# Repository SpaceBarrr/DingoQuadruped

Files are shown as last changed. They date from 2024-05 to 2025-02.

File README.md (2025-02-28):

# Kelpie Quadruped

<p align="center">
    
</p>

## Overview
This repository hosts the code for the Kelpie Quadruped, a robot designed to be low-cost yet capable of both education and research usage and being extensively modified with additional actuators and sensors. CAD for the Kelpie can be found [here](https://grabcad.com/library/kelpie-quadruped-1). A full bill of materials for purchasable components can be found within this repo.
A brief overview of the Kelpie can be found [here](https://www.youtube.com/watch?v=VYclMd-JAFM&ab_channel=SpaceBar).

This code is based on the [Dingo Quadruped](https://github.com/MonashRobotics/DingoQuadruped) codebases, with extensive modifications, including integration into ROS 1 Noetic.

The repository includes a driver node, dingo_driver.py, which should be used anytime the code is run. This file enables joystick control of the Dingo, and allows joint and/or task space commands generated by any other code to be passed through the driver via the appropriate ROS command topics. The joystick can also be toggled on and off to override commands received via ROS command topics

The repo also includes a WeBots simulation of the Kelpie, based on URDF file and meshes which are also provided.

## How Kelpie ROS Network Works
The following flow diagram shows a simplified overview of how a joystick command is handled by the driver to affect joint movements:
<p align="center">
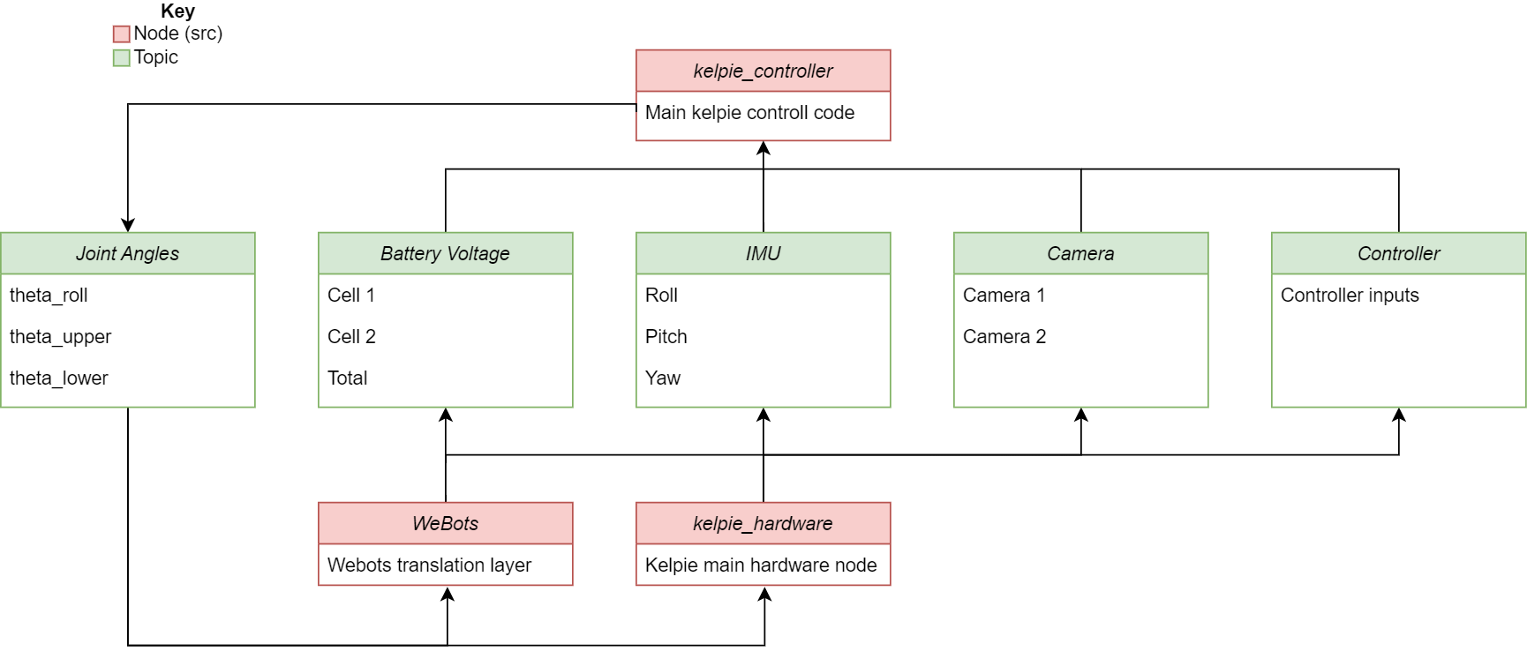
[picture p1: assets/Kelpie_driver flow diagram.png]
    
</p>

## Installation of Code
### Natively
- Install Ubuntu 20.04 onto the Pi's SD card via the [Raspberry Pi Imager](https://www.raspberrypi.com/software/), and setup username, password and network information.
- Install [ros-noetic](http://wiki.ros.org/noetic/Installation/Ubuntu)
- Install necessary packages via `sudo apt-get install python3-catkin-tools git python3-rosdep python3-rosinstall python3-rosinstall-generator python3-wstool python3-pip build-essential wireless-tools libraspberrypi-bin ros-noetic-joy ros-noetic-catkin python3-catkin-tools i2c-tools libi2c-dev python3-smbus`
- Install necessary python packages via `pip install spidev transforms3d pillow rpi.gpio pyserial simple-pid`
- Change directory to the home folder: `cd ~`
- Get a list of available time zones: `timedatectl list-timezones`
- Set local time zone from list e.g: `sudo timedatectl set-timezone Australia/Melbourne`
- Clone this (the Kelpie Quadruped) repository using git: `git clone ...`
- Update all submodules: `git submodule update --init`
- Move into the kelpie_ws folder: `cd /DingoQuadruped/kelpie_ws`
- Initialise rosdep: `sudo rosdep init`
- Fetch dependencies with rosdep: `rosdep update`
- Build the workspace: `catkin build`
- Source the workspace: `source devel/setup.bash`
- Set ROS_MASTER_URI: `echo "export ROS_MASTER_URI=http://dingo:11311" >> ~/.bashrc`
- Source ROS in bashrc .bashrc:`echo "source /opt/ros/noetic/setup.bash" >> ~/.bashrc`, `source ~/.bashrc`
- (Optional) Add a line to .bashrc to automatically source the workspace: `echo "source ~/DingoQuadruped/kelpie_ws/devel/setup.bash" >> ~/.bashrc`, `source ~/.bashrc`

### Additional Installation Steps
#### Bluetooth Setup
For getting bluetooth controller working (for instance PS4 controller)
- More info here: https://www.makeuseof.com/manage-bluetooth-linux-with-bluetoothctl/
- Install bluetooth: 
    - `sudo apt-get install bluetooth bluez bluez-tools`
    - `sudo apt-get install pi-bluetooth`
- To pair and connect a controller:
    - `bluetoothctl`
    - `scan on`
    - `trust AA:BB:CC:11:22:33` (example device)
    - `pair AA:BB:CC:11:22:33` 
    - `connect AA:BB:CC:11:22:33`
- To test the controller:
    - `jstest /dev/input/js0`
- To list connected devices:
    - `bluetoothctl paired-devices`
- To later forget the controller:
    - `bluetoothctl remove AA:BB:CC:11:22:33`

At this stage, the controller will only connect if you run `bluetoothctl` in the terminal, and then press the pair button on the controller. To bypass the step of running `bluetoothctl`, do the following:
- Create a shell script called connect_controller.sh (Make a note of where you create it) with the following contents:
```.
#!/bin/bash

# Replace 'XX:XX:XX:XX:XX:XX' with your controller's MAC address
controller_mac="XX:XX:XX:XX:XX:XX"

# Use bluetoothctl to connect the controller
bluetoothctl <<EOF
connect $controller_mac
exit
EOF`
```
- Make it executable by running `chmod +x connect_controller.sh`
- Create a UDEV rule to run this script every time the controller attempts to pair: `SUBSYSTEM=="bluetooth", KERNEL=="hci0", ACTION=="add", ENV{DEVTYPE}=="adapter", TAG+="systemd", SYMLINK+="bluetooth", RUN+="/bin/sleep 10", RUN+="/path/to/connect_controller.sh"`
- reload the UDEV rules: `sudo udevadm control --reload`
The controller should now autopair every time the pair button is pressed, without needing to do anything on the Pi

#### Wifi Setup
To get WiFi working
- Edit the file /etc/netplan/50-cloud-init.yaml 
- Add the following to the bottom of the file
```.   
    wifis:
        wlan0:
            optional: true
            dhcp4: true
            access-points:
                "<wifi SSID>":
                    password: "<wifi password>"
```

#### LCD Node Additional Setup
The LCD node has been created following the waveshare tutorial here: https://www.waveshare.com/wiki/1.47inch_LCD_Module. Apart from installing the libraries listed there, the fonts also need to be moved into the ubuntu fonts folder to be used by executing the following lines:
- `cd ~`
- `sudo apt-get install unzip -y`
- `sudo wget https://files.waveshare.com/upload/8/8d/LCD_Module_RPI_code.zip`
- `sudo unzip ./LCD_Module_RPI_code.zip`
- `cd ~/LCD_Module_RPI_code/RaspberryPi/python/Font`
- `sudo mv Font00.ttf /usr/share/fonts/truetype/Font00.ttf`
- `sudo mv Font01.ttf /usr/share/fonts/truetype/Font01.ttf`
- `sudo mv Font02.ttf /usr/share/fonts/truetype/Font02.ttf`

If getting an error with "rounded_rectangle", need to install later version of Pillow.
- Upgrade pillow with `pip3 install --upgrade Pillow`

#### Setting necessary permissions for ROS
To run ROS as non-root, must set permissions correctly via udev for several /dev files.
- Add the following to /etc/udev/rules.d/99-ROS.rules
```.   
       KERNEL=="ttyS0", OWNER="root", GROUP="ros", MODE="0660"
       KERNEL=="spi", OWNER="root", GROUP="ros", MODE="0660"
       KERNEL=="i2c", OWNER="root", GROUP="ros", MODE="0660"
       KERNEL=="gpiomem", OWNER="root", GROUP="ros", MODE="0660"
       KERNEL=="mem", OWNER="root", GROUP="ros", MODE="0660"
```
- Add new group to user account: `sudo groupadd ros && sudo adduser <username> ros`
- Reload udev rules: `sudo udevadm control --reload-rules && sudo udevadm trigger`

#### Setting up I2C
- First, run this command to check whether i2c is working for root: `sudo i2cdetect -y 1`. If this doesnt work, try replacing the 1 with a 0. If this works, replace the 1 with a 0 in all subsequent steps.
- Now try for your user: `i2cdetect -y 1`. If the same matrix appears, all is good. Otherwise, run the following:
```.
    sudo groupadd i2c
    sudo chown :i2c /dev/i2c-1
    sudo chmod g+rw /dev/i2c-1
    sudo usermod -aG i2c [INSERT YOUR USERNAME]
```
- Reboot or logout and back in and then check if i2c is working by running `i2cdetect -y 1`. The matrix should now appear for your user.

#### Setting up SPI
Please run the code first before following these steps. If you do not receive an SPI permission error, there is no need to do the following SPI setup steps. Proceed if you receive an error
- Run `ls -la /dev/spidev*` to list SPI devices
- Then, run the following to give your user SPI permissions, repeating the last two lines for all SPI devices listed from previous command:
```.
    sudo groupadd spi
    sudo usermod -aG spi <yourusername>
    sudo chown :spi <put the spi device name here>
    sudo chmod g+rw <put the spi device name here>
```
- Try running the code again. If it works, reboot the device and run the code again immediately after logging in. If it still works after reboot, no need to continue, but it if does not, keep going below:
- Run `sudo nano /etc/systemd/system/spi-permissions.service` and put the following into the file, saving and exiting afterwards:
```.
    [Unit]
    Description=Set SPI Permissions
     
    [Service]
    ExecStart=/path/to/your/script.sh
    User=root
    Group=root
    Restart=on-failure
    RestartSec=5s
     
    [Install]
    WantedBy=multi-user.target
```
- Now, run `nano ~/startspi.sh` and put the following into the file, saving and exiting afterwards. Note: If your SPI device names are different, please update them accordingly:
```.
    #!/bin/bash
    sudo usermod -aG spi <yourusername>
    sudo chown :spi /dev/spidev0.0
    sudo chmod g+rw /dev/spidev0.0
    sudo chown :spi /dev/spidev0.1
    sudo chmod g+rw /dev/spidev0.1
```
- Run the following in the terminal:
    - `sudo chmod +x /path/to/your/script.sh`
    - `sudo systemctl daemon-reload`
    - `sudo systemctl enable spi-permissions.service`
    - `sudo systemctl start spi-permissions.service`

SPI should now work across restarts

#### Setting up Voltage Monitoring
The voltage monitoring on this robot was done using the TLA2024IRUGT chip. Please install the required library to run it with `pip3 install adafruit-circuitpython-tla202x`

#### Setting up camera
- Install required packages: `sudo apt-get install ros-noetic-video-stream-opencv`

#### Configuring web server
- Install apache `sudo apt-get install apache2
`
- Start apache `sudo /etc/init.d/apache2 start`
- Edit the apache conf to point to the Kelpie HTML files and allow access `sudo nano /etc/apache2/sites-enabled/000-default.conf`
    - Change `/var/www` to `home/{username}/DingoQuadruped/web_gui/`
    - Add in the directory directives to allow access
        ```
        <Directory home/{username}/DingoQuadruped/web_gui>
            Options Indexes FollowSymLinks
            AllowOverride All
            Require all granted
        </Directory>
        ```
- Restart apache `sudo /etc/init.d/apache2 restart`
- Install ROS bridge `sudo apt-get install ros-noetic-rosbridge-suite`
- Finally, the web server should be accessible on the local network at http://dingo:80/index.html

#### SD Card Backup
It's a good idea to backup the sdcard every so often. Here is how to do that on linux.
- Take out the sdcard from the Raspberry Pi and mount it into another linux system.
- Run these commands to backup/restore. Replace source/destination appropriately.
    - Backup to file: `sudo dd if=/dev/sdb of=~/kelpie_backup.img bs=4M status=progress`
    - Restore back to sdcard: `sudo dd if=kelpie_backup of=/dev/sdb bs=4M status=progress`

#### Servo Calibration
Help with getting the servos calibrated
 - Run the `calibrate_servo.py` file in the following path: `kelpie_ws\src\kelpie_hardware_interface\scripts\calibrate_servo.py`
 - For auto calibration, type `auto`, this will calibrate all the legs automatically, excluding the roll servos
 - For manual calibration, type the servo name (e.g. `fr r` for front right, roll), then follow the instructions to fine tune the servos
 - Type `q` to save the quit the calibration script

## Running the code
### Kelpie_Driver
The Kelpie_Driver should be started before any other code is launched on the Kelpie. It starts joystick control of the robot and allows joint and task space commands to be received from other code or controllers via command ROS topics, as long as joystick control is disabled. If enabled, joystick control will override any commands sent through the command topics. To launch it, run the following line:
`roslaunch kelpie kelpie.launch`

Arguments are:
- mode (0/1)
    - 0: physical (default)
    - 1: simulation
- input_type (0/1): 
    - 0: PS4 controller (default)
    - 1: keyboard
- use_cam (0/1): 
    - 0: camera off (default)
    - 1: camera on (Note that this is induces lag on a Pi4, recommend Pi 5)

With no arguments specified, it will assume a joystick controller is used for control and it will launch the hardware interface with IMU feedback disabled. No joint data will be published for WeBots to use to simulate the robot.

As an example of how the arguments can be used, if the code is to be run with keyboard control and the camera enabled, you would launch the driver with the following arguments: 
`roslaunch kelpie kelpie.launch input_type:=1 use_cam:=1`

When the code is running, the device that is ssh'd into the Kelpie quadruped, you can go to http://dingo:80/index.html to access the gui.

### Kelpie Joystick Controls
<p align="center">
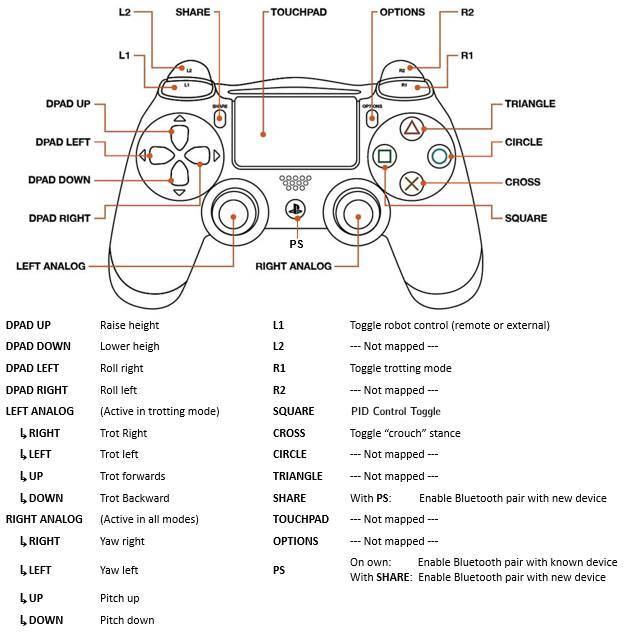
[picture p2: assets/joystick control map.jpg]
    
</p>

The diagram above shows the mapping of joystick commands for the Kelpie. These instructions are based on a PS4 type controller. An alternative, more general description of joystick commands is below:

The Kelpie has two main states: Rest and Trot. 
- While in the TROT state: Left stick controls the robot's movement. Right stick controls the robot's tilt and turning. PID control only applies to the yaw.
- While in the REST state: Left stick is disabled. Right stick controls the robot's gaze while staying in place. PID control can be toggled.

Buttons:
- Joystick Control Toggle (L1 Button): Pause/Resume control from the joystick.
- Gait Toggle (R1 Button): Toggles between trotting and resting modes.
- PID Control Toggle (Square): Toggles PID control on/off

Movement: (Speed proportional to how far stick is moved)
- Left Stick (Horizontal): Pushing left or right strafes the robot in that direction.
- Left Stick (Vertical): Push up to move forward, down to move backward.

Gaze:
- Right Stick (Horizontal): Pushing left or right turns the robot in that direction.
- Right Stick (Vertical): Push up to raise front of robot, down to raise back of robot.

Orientation:
- D-pad (Vertical): Pressing up or down adjusts the height of the robot.
- D-pad (Horizontal): Pressing left or right tilts the robot in that direction.

## Running the Simulation on WeBots
### For Windows users (Native Linux users can skip this)
- Install Windows Subsystem for Linux (WSL) for Ubuntu 20.04 by running `wsl --install -d Ubuntu-20.04` in your preferred terminal
- From Powershell, type in `wsl` (`wsl -d Ubuntu-20.04` if you have multiple ubuntu versions), this will launch WSL and Ubuntu 20.04

### Install Required Packages
- Execute the following in the bash terminal:
```
sudo apt-get update
sudo sh -c 'echo "deb http://packages.ros.org/ros/ubuntu $(lsb_release -sc) main" > /etc/apt/sources.list.d/ros-latest.list'
sudo apt install curl
curl -s https://raw.githubusercontent.com/ros/rosdistro/master/ros.asc | sudo apt-key add -
sudo apt-get update
sudo mkdir -p /etc/apt/keyrings
cd /etc/apt/keyrings
sudo wget -q https://cyberbotics.com/Cyberbotics.asc
echo "deb [arch=amd64 signed-by=/etc/apt/keyrings/Cyberbotics.asc] https://cyberbotics.com/debian binary-amd64/" | sudo tee /etc/apt/sources.list.d/Cyberbotics.list
sudo apt update
sudo apt install webots
sudo apt-get install ros-noetic-desktop-full ros-noetic-moveit
sudo apt-get install python3-rosdep
sudo rosdep init
rosdep update
sudo apt-get install ros-noetic-webots-ros ros-noetic-joy python3-pip
pip3 install transforms3d adafruit-circuitpython-servokit adafruit-circuitpython-bno055
sudo apt install python-is-python3
```
### Setting Up the Simulation Environment
- Source the ros files on the shell launch and other environment variables, **don't forget to change the file path** (make sure the path is WSL and not windows)
```
echo "source /opt/ros/noetic/setup.bash" >> ~/.bashrc
echo "export KELPIE_WS=/mnt/windows/path/to/kelpie_ws" >> ~/.bashrc
echo "export WEBOTS_HOME=/usr/local/webots" >> ~/.bashrc
source ~/.bashrc
```
- Set up the workspace
```
cd /path/to/kelpie_ws
catkin_make
```

### Running the Simulation Environment
- Run the kelpie launch file on a local ubuntu 20.04 environment.
```
cd /path/to/kelpie_ws
catkin_make
source devel/setup.bash
roslaunch src/kelpie/launch/kelpie.launch mode:=1
```
- Open another terminal and run the webots launch file
```
source devel/setup.bash
roslaunch src/kelpie_webots/launch/webots_ros_python.launch 
```

### Running the Simulation as a Digital Twin
- Connect to the kelpie and run it as described in [Kelpie_Driver](#kelpie_driver), in physical mode
```
roslaunch src/kelpie/launch/kelpie.launch mode:=0
```
- Run the webots launch file on your local (Ubuntu!) computer
```
cd /path/to/kelpie_ws
catkin_make
source devel/setup.bash
export ROS_MASTER_URI=http://dingo.local:11311/
roslaunch src/kelpie_webots/launch/webots_ros_python.launch 
```

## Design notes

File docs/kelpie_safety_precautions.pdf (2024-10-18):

# The Kelpie Safety Precautions

Manufacturing
- Do not touch the 3D printer nozzle when printing
- Be careful when taking off the supports from the 3D printed parts as they may be sharp

Operation
- Do not touch the servos when the robot it powered as it may get hot
- Avoid getting too close to the robot when in motion as you may get hit/pinched
- Do not use a LiPo battery when it is overcharged or undercharged

Storing
- Do not leave the LiPo battery in the robot when storing
- Always discharge the battery and store it in a safe location

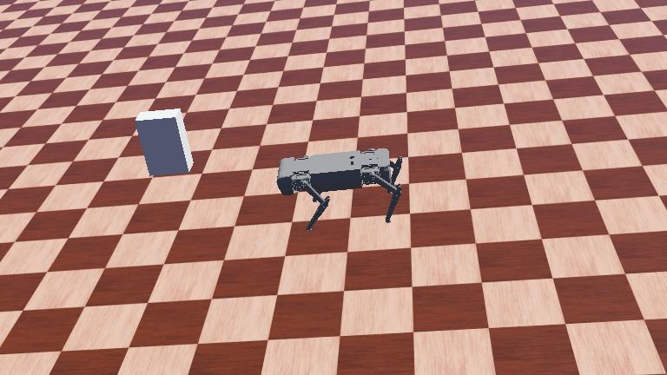
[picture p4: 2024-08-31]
kelpie_ws/src/kelpie_webots/launch/webots/worlds/.kelpie_default.jpg

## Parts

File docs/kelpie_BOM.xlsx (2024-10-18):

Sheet: Kelpie BOM
Category | Item | Link | Comments | Quantity | Price per item | Total Price
Leg Linkage Mechanism | Servo Motors | https://www.aliexpress.com/item/1005004670681332.html?spm=a2g0o.cart.0.0.35d338daLsP2P7&mp=1 | 180 degrees, 35kg | 12 | 44.48916667 | 533.87
 | Servo Horns | https://www.aliexpress.com/item/1005001485067326.html | RC Car Steering Servo Horn Arm 25T Teeth Long | 4 | 2.36 | 9.44
 | Servo Discs | https://www.aliexpress.com/item/32827000998.html?scm_id=1007.23125.137358.0&scm-url=1007.23125.137358.0 | 10 pcs, with screws. | 1 | 6.54 | 6.54
 | Heatsinks | https://vi.aliexpress.com/item/1005005848003793.html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 | Heat sinks for servos, cut in half for each | 4 | 0.38 | 1.52
 | Thermal tape | https://www.amazon.com.au/dp/B087D48T61?ref=ppx_pop_mob_ap_share | Thermal tape for servos, cut to size | 1 | 14.75 | 14.75
 | Threaded rods (Long) | https://www.aliexpress.com/item/1005004660730267.html?spm=a2g0o.detail.1000023.16.1569213ad8nkQv | M3 x 110mm (5pcs) | 1 | 1.26 | 1.26
 | Threaded rods,short | https://www.aliexpress.com/item/1005004660730267.html?spm=a2g0o.detail.1000023.16.1569213ad8nkQv | M3 x 25 (5pcs) | 1 | 1.14 | 1.14
 | Rod ends (Long) | https://www.aliexpress.com/item/32878321408.html?spm=a2g0o.detail.1000023.6.64cd339bFmvU9y | 10pcs, 015 M3 With Screw | 1 | 5.19 | 5.19
 | Rod ends (Short) | https://www.aliexpress.com/item/32878321408.html?spm=a2g0o.detail.1000023.6.64cd339bFmvU9y | 10pcs, 012 M3 With Screw | 1 | 5.19 | 5.19
 | Bearings | https://vi.aliexpress.com/item/1005007293843469.html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 | 10pcs, need 2pcs for each leg | 1 | 5.38 | 5.38
Computing | Raspberry Pi 4 Model B | https://core-electronics.com.au/raspberry-pi-4-model-b-8gb.html | 8gb Ram | 1 | 127.9 | 127.9
 | 32GB MicroSD card | https://core-electronics.com.au/microsd-memory-card-32gb-class-10.html | 32GB is maximum Pi supports | 1 | 19 | 19
 | LCD Screen | https://core-electronics.com.au/147inch-lcd-display-module-rounded-corners-172x320-resolution-spi-interface.html | 1.47 inch | 1 | 19.95 | 19.95
 | Fan | https://au.mouser.com/ProductDetail/Delta-Electronics/AFB0605MC?qs=%2FW4LtXOBxKtFoJ8jJfKvRw%3D%3D | 60x60x13mm dimensions, 5V | 2 | 21.42 | 42.84
Power Supply and Management | 2S LiPo Battery | https://www.auselectronicsdirect.com.au/7.4v-8000mah-2s-50c-li-po-battery-with-ec5-plug?gad_source=1 | 7.4V 8000mAh 2S 50C Li-Po Battery with EC5 Plug | 1 | 94.95 | 94.95
 | Emergency Stop Switch | https://au.mouser.com/ProductDetail/Shin-Chin/R13-930S-01-BR?qs=W%2FMpXkg%252BdQ4sW1BEynCGwA%3D%3D | 21A at 14VDC rated | 1 | 19.27 | 19.27
 | On/off Switch | https://au.mouser.com/ProductDetail/ZF/CRE22F2FBBNE?qs=4EnmSMTL3HO0CsCQiVQQXQ%3D%3D | 20A at 14VDC rated | 1 | 2.76 | 2.76
PCB Manufacturing | Power Distribution Board | - | Check details in PDB BOM sheet | 1 | 112.6926667 | 112.6926667
 | Pi Hat | - | Check details in Pi Hat BOM sheet | 1 | 9.868 | 9.868
Body Construction | Acrylic | https://www.acrylicsonline.com.au/products/matte-black-acrylic-sheet | 3mm acrylic, A2 size (420 x 594mm) | 1 | 22.5 | 22.5
 | Velcro Strap | https://www.amazon.com.au/dp/B000078CUB?ref=ppx_pop_mob_ap_share | Velcro strap for handle | 1 | 12.85 | 12.85
 | M3 Inserts (Self Tapping) | https://vi.aliexpress.com/item/1005003522894174.html | 20pcs | 2 | 5.79 | 11.58
Misc | [OPTIONAL] PS4 Controller | https://www.jbhifi.com.au/products/ps4-playstation-4-dualshock-4-wireless-controller-black | Lab already has controllers and the robot can be keyboard controlled, so not counted | 1 | 79 | 79
NOTE: AS THE FOLLOWING ITEMS ARE SOLD IN MUCH LARGER QUANTITIES THAN NEEDED, AND ARE OFTEN ALREADY AVAILABLE TO THE BUILDER, THEIR COST HAS BEEN REDUCED TO THE AMOUNT ACTUALLY NEEDED TO BUILD THE QUADRUPED
Body Construction | PLA Filament | https://www.rmcomponents.com.au/products/pla-3d-printer-filament-red-green-orange-black-and-white-color-250g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 | 1kg spool, approx. 2kg needed | 2 | 24 | 48
 | ABS Filament | https://www.rmcomponents.com.au/products/abs-3d-printer-filament-red-green-orange-black-and-white-color-250g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 | 250g spool, approx. 150g needed | 0.6 | 7.84 | 4.704
 | TPU Filament | https://www.rmcomponents.com.au/products/3d-printer-filament-tpu-red-green-blue-yellow-and-orange-color-250g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 | 250g spool, approx. 50g needed | 0.2 | 11.79 | 2.358
 |  |  |  |  | Total Cost | 1214.502667

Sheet: PDB BOM
Category | Item | Link | Comments | Quantity | Price per item | Total Price
Headers | B5P-VH | https://www.digikey.com.au/en/products/detail/jst-sales-america-inc/B5P-VH/926550 | CONN HEADER VERT 5POS 3.96MM (for raspberry pi and other addons) | 5 | 0.58 | 2.9
 | BM05B-GHS-TBT | https://www.digikey.com.au/en/products/detail/jst-sales-america-inc/BM05B-GHS-TBT/807803 | CONN HEADER SMD 5POS 1.25MM (for I2C) | 3 | 0.83 | 2.49
 | S3B-XH-A | https://www.digikey.com.au/en/products/detail/jst-sales-america-inc/S3B-XH-A/1651048 | CONN HEADER R/A 3POS 2.5MM (for LiPo balance lead) | 1 | 0.31 | 0.31
 | BM02B-GHS-TBT | https://www.digikey.com.au/en/products/detail/jst-sales-america-inc/BM02B-GHS-TBT/807800 | CONN HEADER SMD 2POS 1.25MM | 1 | 0.62 | 0.62
 | HTSW-101-08-G-T-RA | https://au.mouser.com/ProductDetail/200-HTSW10108GTRA | Headers & Wire Housings High Temperature PCB Header Strips, 0.100" pitch (for servos) | 12 | 0.958 | 11.496
 | Female XT60 Connector | https://vi.aliexpress.com/item/1005006084779029.html?mp=1 | XT60PT Connector Plug Female, 10pcs | 0.1 | 9.09 | 0.909
 | Male XT60 Connector | https://vi.aliexpress.com/item/1005006084779029.html?mp=1 | XT60PT Connector Plug Male, 10pcs | 0.1 | 9.09 | 0.909
Integrated Circuits (ICs) | 3.3V Voltage Regulator (AP7370-33W5-7) | https://au.mouser.com/ProductDetail/621-AP7370-33W5-7 | LDO Voltage Regulators 300mA, 3.3V ULDO Regulator | 1 | 0.644 | 0.644
 | 5V Voltage Regulator (RT6258CGQUF) | https://au.mouser.com/ProductDetail/835-RT6258CGQUF | Switching Voltage Regulators 8A, 23V Synchronous Step-Down Converter with 3.3V/5V LDO | 1 | 4.58 | 4.58
 | Current Monitor (INA3221AIRGVR) | https://au.mouser.com/ProductDetail/595-INA3221AIRGVR | Current & Power Monitors & Regulators Triple Channel Shunt & Bus Vltg Monitor | 4 | 5.87 | 23.48
 | Servo Driver (PCA9685PW,112) | https://au.mouser.com/ProductDetail/771-PCA9685PW%2c112 | LED Display Drivers I2C Bus LED Controller 28-Pin | 1 | 3.5 | 3.5
 | ADC Converter (TLA2024IRUGT) | https://au.mouser.com/ProductDetail/595-TLA2024IRUGT | Analog to Digital Converters - ADC 12-bit, 4-channel, delta-sigma ADC with voltage reference, oscillator, PGA and I2C 10-X2QFN -40 to 85 | 1 | 3.69 | 3.69
 | IMU (LSM6DSV16XTR) | https://www.mouser.com/ProductDetail/511-LSM6DSV16XTR | IMUs - Inertial Measurement Units iNEMO 3D accelerometer and 3D gyroscope: always-on inertial module embed machine | 1 | 5.13 | 5.13
Resistors | 10mΩ Resistor | https://au.mouser.com/ProductDetail/667-ERJ-8CWFR010V | Current Sense Resistors - SMD 1206 10mohm 1% Curr Sense AEC-Q200 | 12 | 0.911 | 10.932
 | 10Ω Resistor | https://au.mouser.com/ProductDetail/603-RC0603FR-0710RL | Thick Film Resistors - SMD 10 Ohms 100mW 0603 1% | 1 | 0.157 | 0.157
 | 300Ω Resistor | https://www.mouser.com/ProductDetail/603-RT0603DRD07300RL | Thin Film Resistors - SMD 300 OHM .5% 25PPM 1/10W | 1 | 0.1 | 0.1
 | 1kΩ Resistor | https://au.mouser.com/ProductDetail/667-ERJ-3GEYJ102V | Thick Film Resistors - SMD 0603 1Kohms 5% AEC-Q200 | 2 | 0.157 | 0.314
 | 8.2kΩ Resistor | https://au.mouser.com/ProductDetail/603-RC0603FR-078K2L | Thick Film Resistors - SMD 8.2 kOhms 100 mW 0603 1% | 1 | 0.157 | 0.157
 | 10k Resistor | https://au.mouser.com/ProductDetail/667-ERA-3AEB103V | Thin Film Resistors - SMD 0603 1/10W 10Kohms 0.1% 25ppm | 8 | 0.22 | 1.76
Capacitors | 10pF Capacitor | https://au.mouser.com/ProductDetail/810-C1608C0G1H100D | Multilayer Ceramic Capacitors MLCC - SMD/SMT 0603 50VDC 10pF C0G 0.8mm | 1 | 0.173 | 0.173
 | 0.1uF Capacitor | https://au.mouser.com/ProductDetail/80-C0603X104K5R | Multilayer Ceramic Capacitors MLCC - SMD/SMT 50V 0.1uF X7R 0603 10% Flex Soft | 12 | 0.22 | 2.64
 | 0.47uF Capacitor | https://au.mouser.com/ProductDetail/81-GRM188R71C474KA88 | Multilayer Ceramic Capacitors MLCC - SMD/SMT 0.47 uF 16 VDC 10% 0603 X7R | 3 | 0.188 | 0.564
 | 1uF Capacitor | https://au.mouser.com/ProductDetail/581-0603ZD105K | Multilayer Ceramic Capacitors MLCC - SMD/SMT KGM15BR51A105KT NEW GLOBAL PN 10V 1uF X5 A 581-KGM15BR51A105KT | 3 | 0.157 | 0.471
 | 4.7uF Capacitor | https://au.mouser.com/ProductDetail/187-CL10A475KP8NNWC | Multilayer Ceramic Capacitors MLCC - SMD/SMT 4.7uF X5R +/-10% 10v 0603 | 1 | 0.157 | 0.157
 | 10uF Capacitor | https://au.mouser.com/ProductDetail/963-LMK107BBJ106MALT | Multilayer Ceramic Capacitors MLCC - SMD/SMT 963-MSASL168BB5106MT RPLCMT PN 10V 10uF X5R 0603 20% | 3 | 0.251 | 0.753
 | 10uF Capacitor (Aluminium Electrolytic) | https://au.mouser.com/ProductDetail/667-EEE-FK1H100P | Aluminium Electrolytic Capacitors - SMD 10uF 50V | 1 | 0.581 | 0.581
 | 22uF Capacitor | https://au.mouser.com/ProductDetail/187-CL10A226MP8NUNE | Multilayer Ceramic Capacitors MLCC - SMD/SMT 22uF+/-20% 10V X5R 1 0603 | 4 | 0.283 | 1.132
Inductors | 1uH Inductor | https://au.mouser.com/ProductDetail/710-744311100 | Power Inductors - SMD WE-HCI 1uH 15A DCR=4.6mOhms AEC-Q200 | 1 | 5.97 | 5.97
Misc | NPN Transistor (MMBT3904) | https://au.mouser.com/ProductDetail/637-MMBT3904 | Bipolar Transistors - BJT BJT, SOT-23, 40V, 200mA, NPN | 1 | 0.173 | 0.173
 | Schottky Diode | https://au.mouser.com/ProductDetail/583-BAT54S | Schottky Diodes & Rectifiers SOT23 0.2A 30V Schot tky Dblr | 1 | 0.48 | 0.48
 | ATO Fuse Holder | https://au.mouser.com/ProductDetail/534-3587TR | Fuse Holder SMT STD Fuse HOLDER TAPE/REEL | 1 | 2.42 | 2.42
 | ATO Fuse | https://www.ebay.com.au/itm/283707768049 | 50A Small ATO Blade Fuse - Pack of 15 | 0.06666666667 | 14.95 | 0.9966666667
 | SMD Fuse | https://au.mouser.com/ProductDetail/576-0805L002YR | Resettable Fuses - PPTC PTC 63V POLYFUSE SURF MOUNT 0805 0.02A | 3 | 1.35 | 4.05
 | Violet LED | https://au.mouser.com/ProductDetail/604-AA3528VRVFS-A | Standard LEDs - SMD Violet Water Clear 250mcd 120 Deg | 1 | 1.02 | 1.02
Manufacturing | PDB Board | https://jlcpcb.com/ | Quoted for 5 boards (USD$3.2) | 0.2 | 4.77 | 0.954
 | SMT Stencil | https://jlcpcb.com/ | Stencil for reflowing PCB (USD$10.78) | 1 | 16.08 | 16.08
 |  |  |  |  | Total Cost | 112.6926667

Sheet: Pi Hat BOM
Category | Item | Link | Comments | Quantity | Price per item | Total Price
Headers | 8 Pos JST GH | https://www.digikey.com.au/en/products/detail/jst-sales-america-inc/BM08B-GHS-TBT/807806 | CONN HEADER SMD 8POS 1.25MM (for display) | 1 | 0.87 | 0.87
 | 5 Pos JST VH | https://vi.aliexpress.com/item/1005005448034046.html?spm=a2g0o.cart.0.0.510pcs/Lot B5PS-VH(LF)(SN) 3.96mm Pitch 5PIN R/A Wire to Board Crimp style Connectors2cc38daWaA0Tp&mp=1&gatewayAdapt=glo2vnm | 10pcs/Lot B5PS-VH(LF)(SN) 3.96mm Pitch 5PIN R/A Wire to Board Crimp style Connectors | 0.1 | 5.29 | 0.529
 | 2x10 Female Pin Header | https://vi.aliexpress.com/item/4000330409245.html?mp=1 | 10PCS 2X3/4/5/6/7/8/10/20/40 PIN Double Row Right Angle Female Pin Header 2.54MM PITCH Strip Connector Socket | 0.1 | 2.77 | 0.277
 | 2x20 Female GPIO Header | https://core-electronics.com.au/gpio-header-for-raspberry-pi-hat-2x20-short-female-header.html | GPIO Header for Raspberry Pi HAT - 2x20 Short Female Header | 1 | 3.9 | 3.9
 | 2x10 Female Pin Header | https://vi.aliexpress.com/item/4000330409245.html?mp=1 | 10PCS 2X3/4/5/6/7/8/10/20/40 PIN Double Row Right Angle Female Pin Header 2.54MM PITCH Strip Connector Socket | 1 | 2.77 | 2.77
Manufacturing | Pi Hat Board | https://jlcpcb.com/ | Quoted for 5 boards (USD$5.1) | 0.2 | 7.61 | 1.522
 |  |  |  |  | Total Cost | 9.868

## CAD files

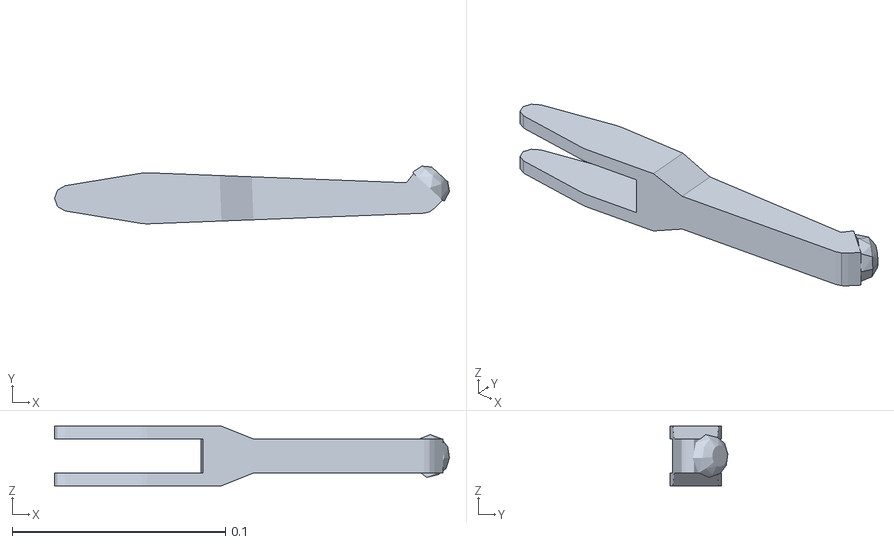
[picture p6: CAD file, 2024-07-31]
kelpie_ws/src/kelpie_webots/launch/webots/klp_urdf/meshes/collision/bac/Body03_coll.stl
0.185 x 0.0271 x 0.028

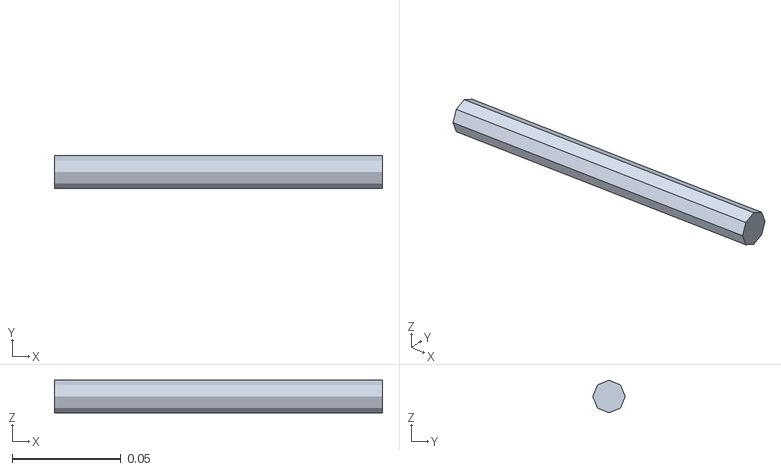
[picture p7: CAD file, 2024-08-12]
kelpie_ws/src/kelpie_webots/launch/webots/klp_urdf/meshes/collision/Body02_coll.stl
0.151 x 0.015 x 0.015

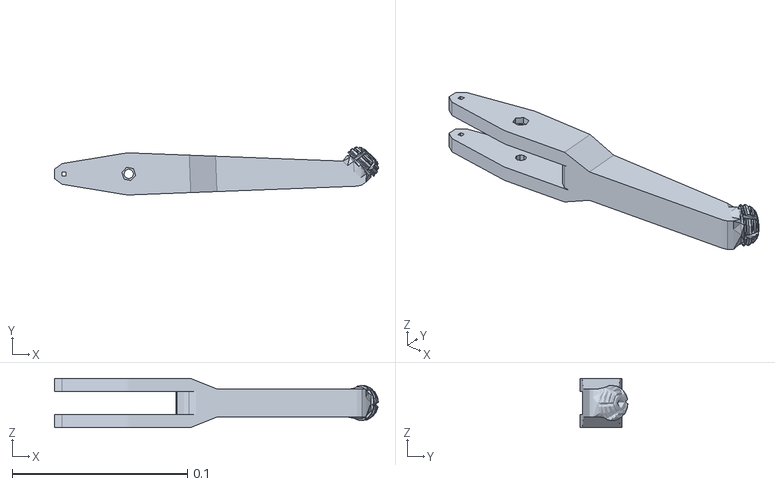
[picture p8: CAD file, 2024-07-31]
kelpie_ws/src/kelpie_webots/launch/webots/klp_urdf/meshes/visual/Body03.stl
0.185 x 0.0273 x 0.028

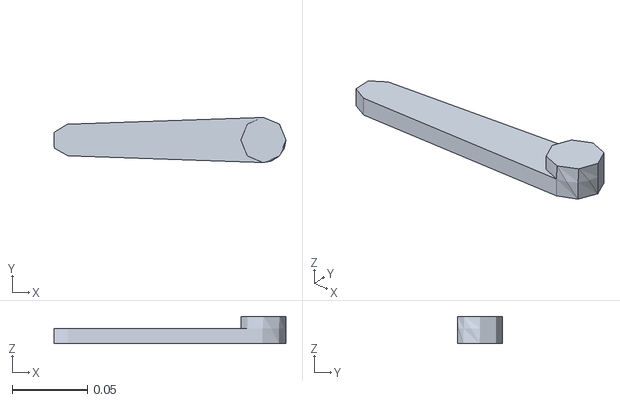
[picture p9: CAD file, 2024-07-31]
kelpie_ws/src/kelpie_webots/launch/webots/klp_urdf/meshes/collision/bac/Body02_coll.stl
0.154 x 0.03 x 0.018

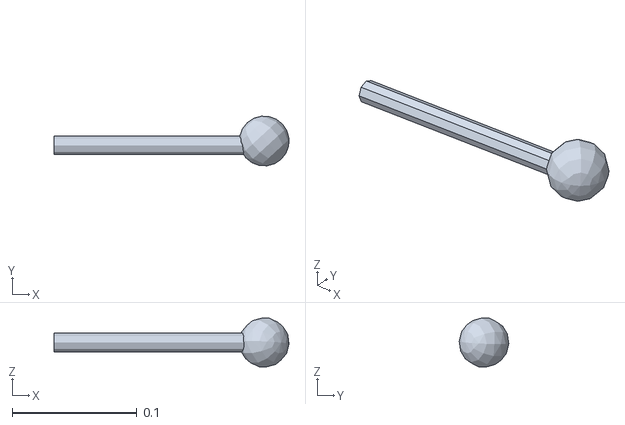
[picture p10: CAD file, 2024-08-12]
kelpie_ws/src/kelpie_webots/launch/webots/klp_urdf/meshes/collision/Body09_coll.stl
0.188 x 0.0397 x 0.0389

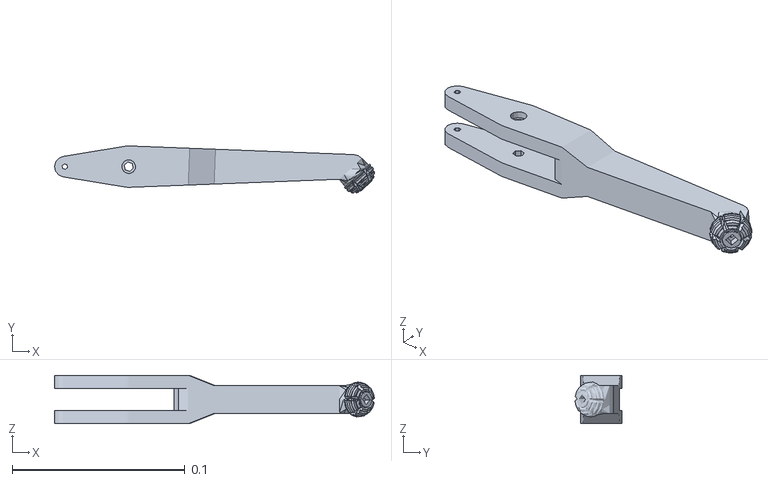
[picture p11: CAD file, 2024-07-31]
kelpie_ws/src/kelpie_webots/launch/webots/klp_urdf/meshes/visual/Body09.stl
0.185 x 0.0273 x 0.028

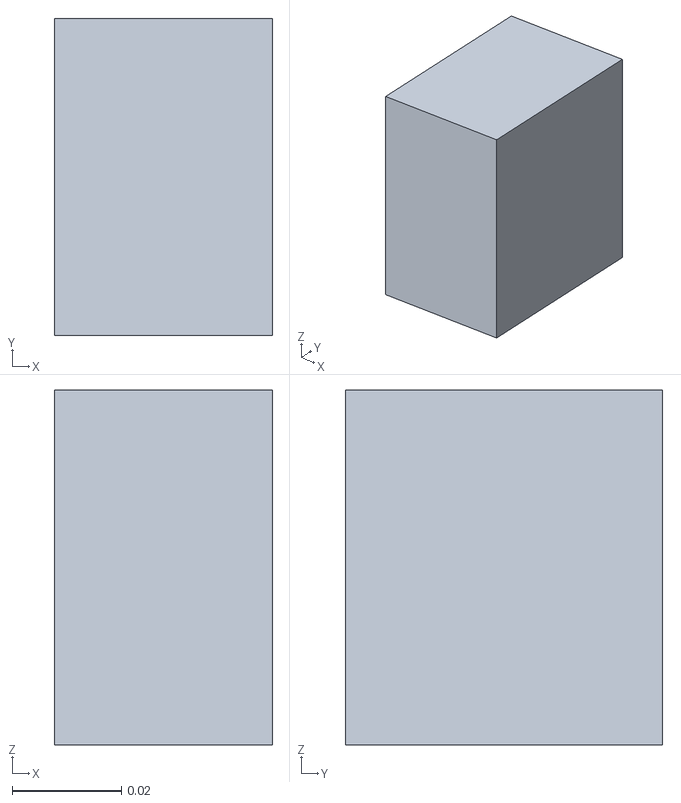
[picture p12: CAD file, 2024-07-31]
kelpie_ws/src/kelpie_webots/launch/webots/klp_urdf/meshes/collision/bac/Body10_coll.stl
0.04 x 0.058 x 0.065

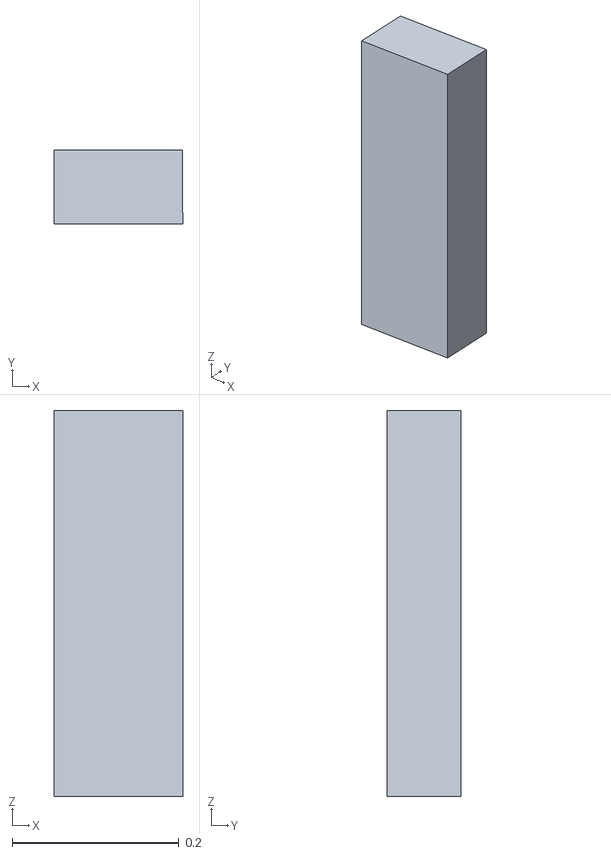
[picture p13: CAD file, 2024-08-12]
kelpie_ws/src/kelpie_webots/launch/webots/klp_urdf/meshes/collision/base_coll.stl
0.154 x 0.089 x 0.463

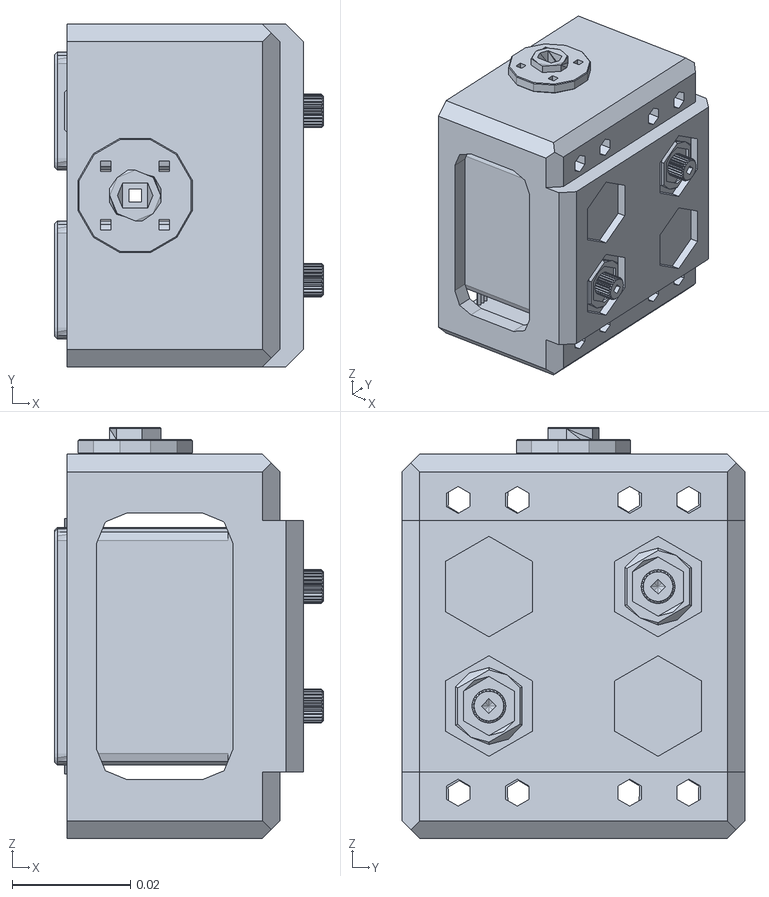
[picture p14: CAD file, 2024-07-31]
kelpie_ws/src/kelpie_webots/launch/webots/klp_urdf/meshes/visual/Body10.stl
0.0455 x 0.058 x 0.0695

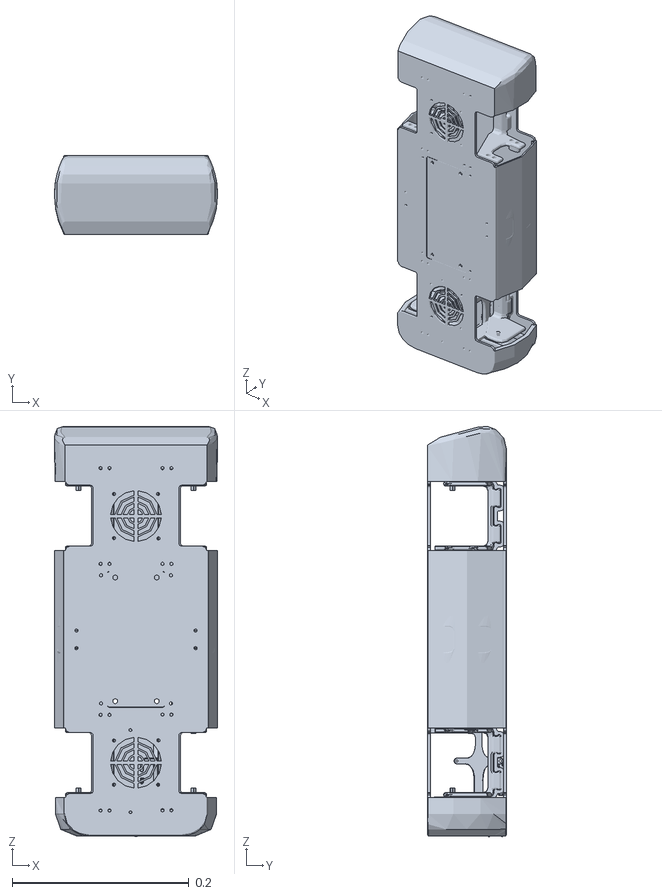
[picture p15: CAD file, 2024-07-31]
kelpie_ws/src/kelpie_webots/launch/webots/klp_urdf/meshes/visual/base.stl
0.185 x 0.089 x 0.464

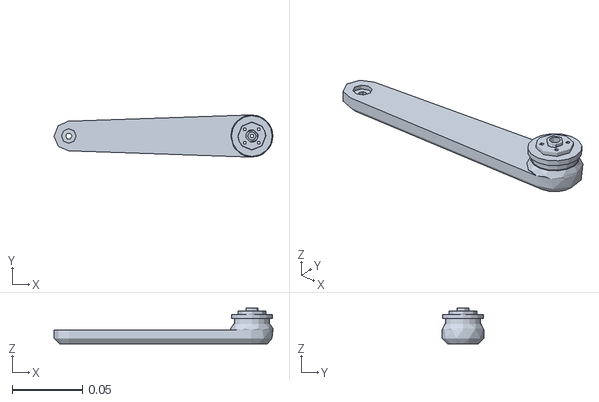
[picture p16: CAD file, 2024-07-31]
kelpie_ws/src/kelpie_webots/launch/webots/klp_urdf/meshes/visual/Body02.stl
0.155 x 0.03 x 0.0255

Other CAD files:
kelpie_ws/src/kelpie_webots/launch/webots/klp_urdf/meshes/collision/bac/Body09_coll.stl
kelpie_ws/src/kelpie_webots/launch/webots/klp_urdf/meshes/collision/Body03_coll.stl
kelpie_ws/src/kelpie_webots/launch/webots/klp_urdf/meshes/collision/bac/Body07_coll.stl
kelpie_ws/src/kelpie_webots/launch/webots/klp_urdf/meshes/visual/Body07.stl
kelpie_ws/src/kelpie_webots/launch/webots/klp_urdf/meshes/collision/bac/Body01_coll.stl
kelpie_ws/src/kelpie_webots/launch/webots/klp_urdf/meshes/collision/bac/Body04_coll.stl
kelpie_ws/src/kelpie_webots/launch/webots/klp_urdf/meshes/visual/Body01.stl
kelpie_ws/src/kelpie_webots/launch/webots/klp_urdf/meshes/collision/bac/base_coll.stl
kelpie_ws/src/kelpie_webots/launch/webots/klp_urdf/meshes/visual/Body04.stl

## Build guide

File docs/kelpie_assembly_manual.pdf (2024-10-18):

# The Kelpie Assembly Manual

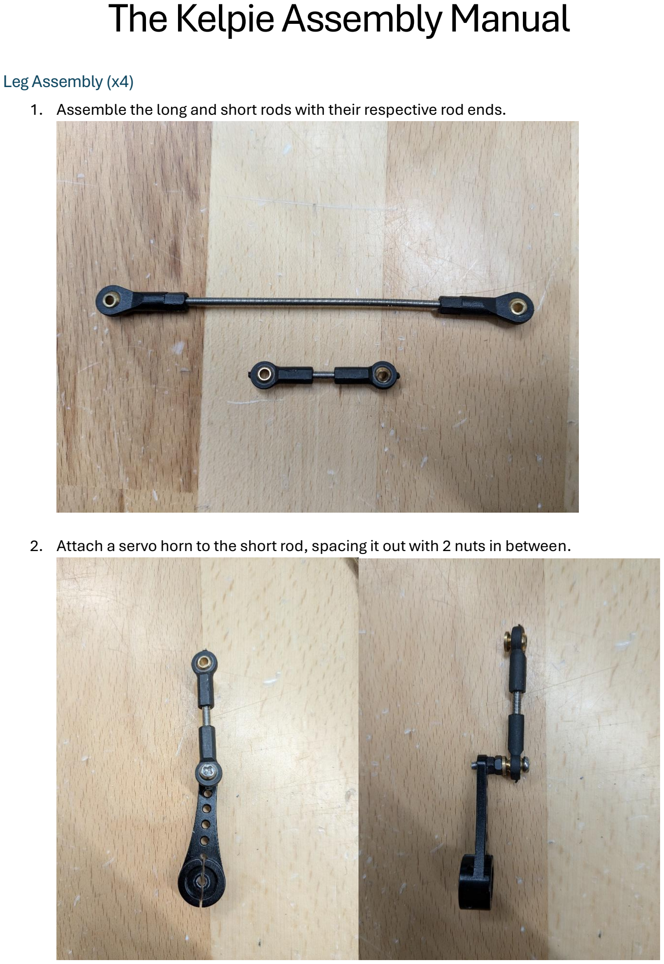
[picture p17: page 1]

Leg Assembly (x4)
1. Assemble the long and short rods with their respective rod ends.
2. Attach a servo horn to the short rod, spacing it out with 2 nuts in between.

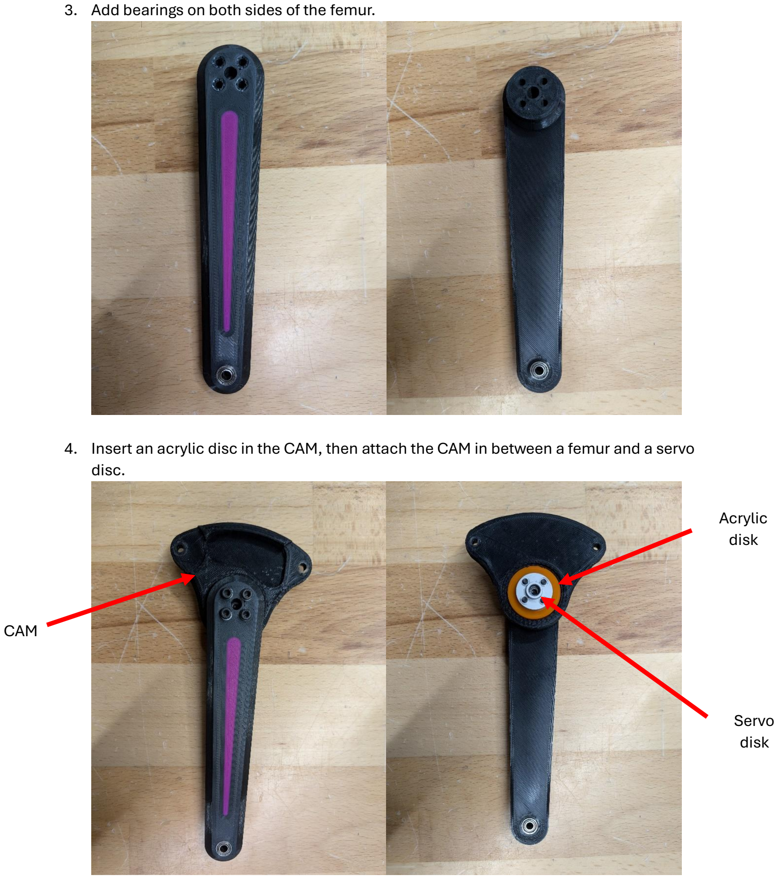
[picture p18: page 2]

3. Add bearings on both sides of the femur.
4. Insert an acrylic disc in the CAM, then attach the CAM in between a femur and a servo disc.

CAM

Acrylic
disk

Servo
disk

5. Screw on the tibia to the femur, then attach the long rod between the femur and cam.

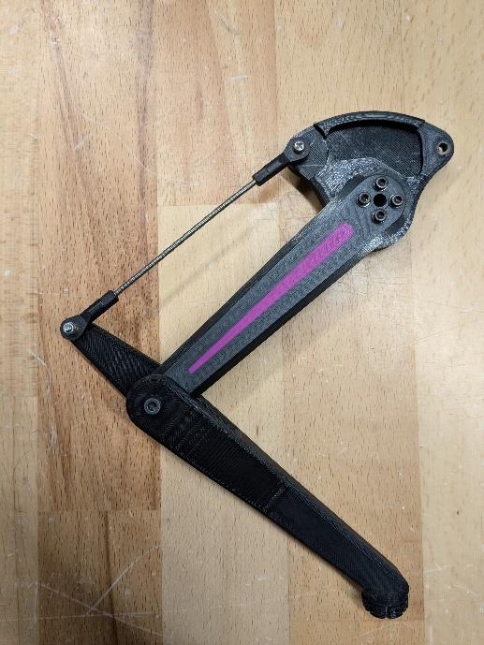
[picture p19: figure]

6. Attach the short rod to the cam.

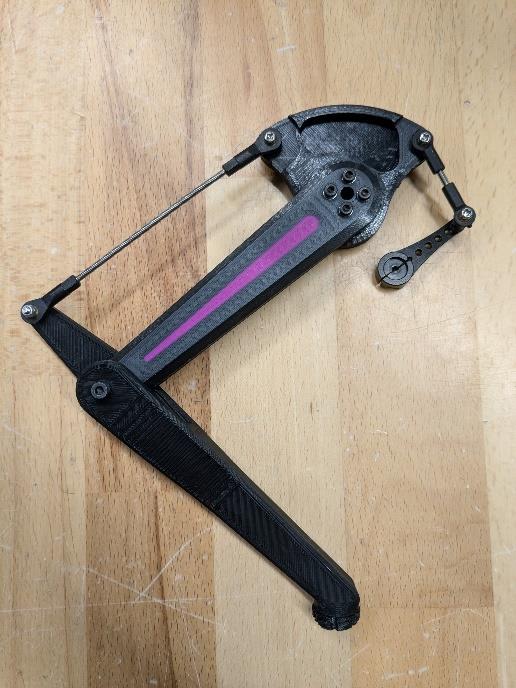
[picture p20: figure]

7. Screw on the roll servo to the side of the servo hub, then screw on the upper and lower servos. Next, put on the heat sinks on the servos.

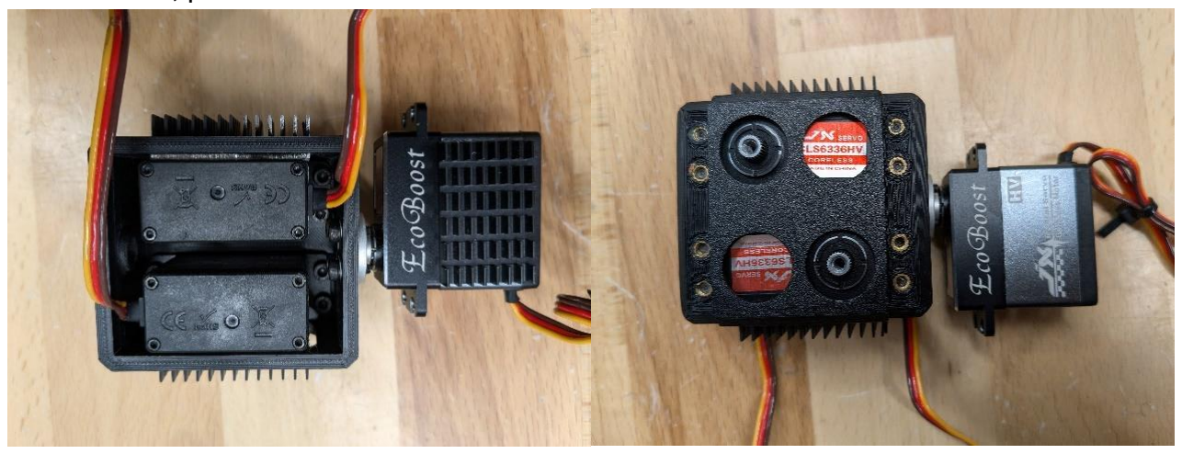
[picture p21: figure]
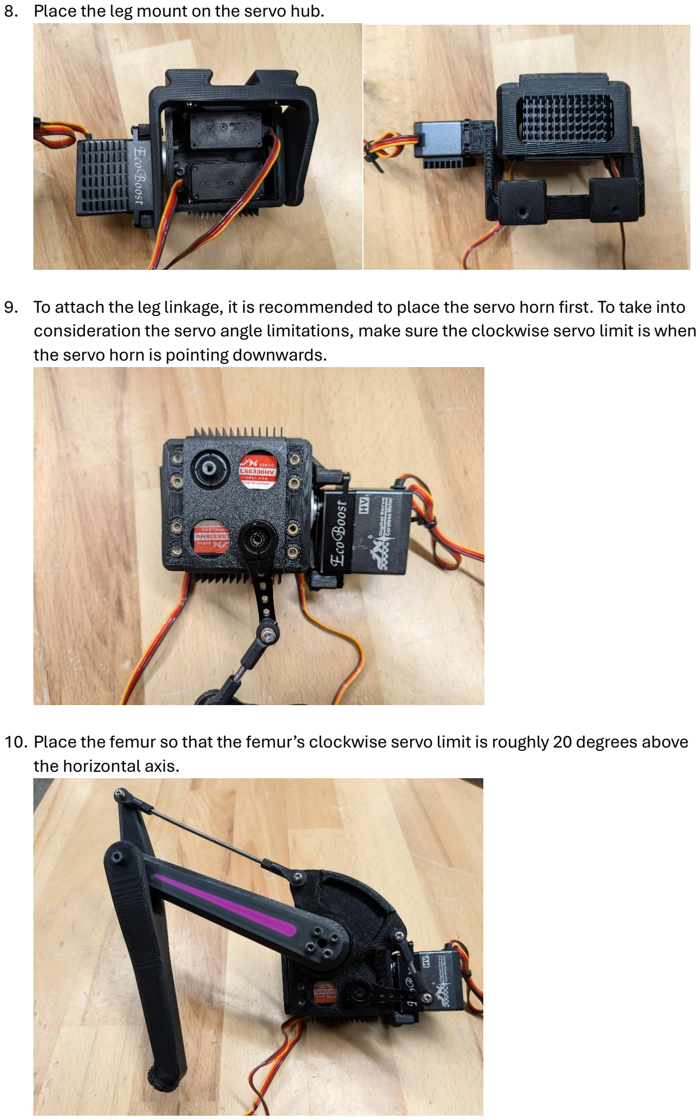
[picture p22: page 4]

8. Place the leg mount on the servo hub.
9. To attach the leg linkage, it is recommended to place the servo horn first. To take into consideration the servo angle limitations, make sure the clockwise servo limit is when the servo horn is pointing downwards.
10. Place the femur so that the femur’s clockwise servo limit is roughly 20 degrees above the horizontal axis.

Battery Hatch Assembly
1. Assemble the battery hatch using the aux mount, slider, and crank. Then attach a rubber band to power the latch mechanism.

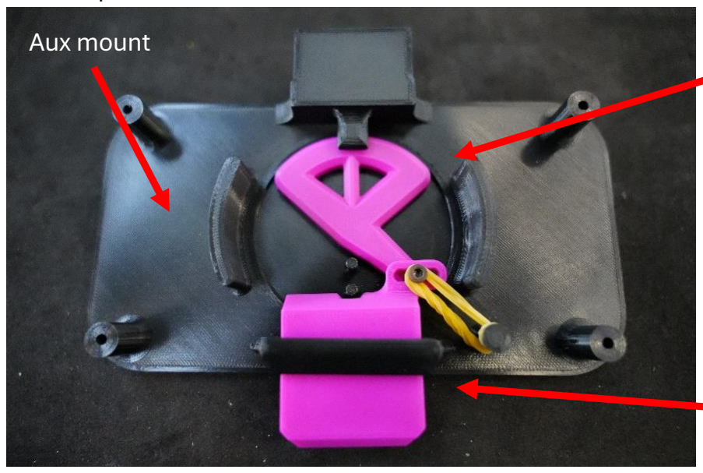
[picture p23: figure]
Aux mount

2. Add the battery cage and handles.

Crank

Slider

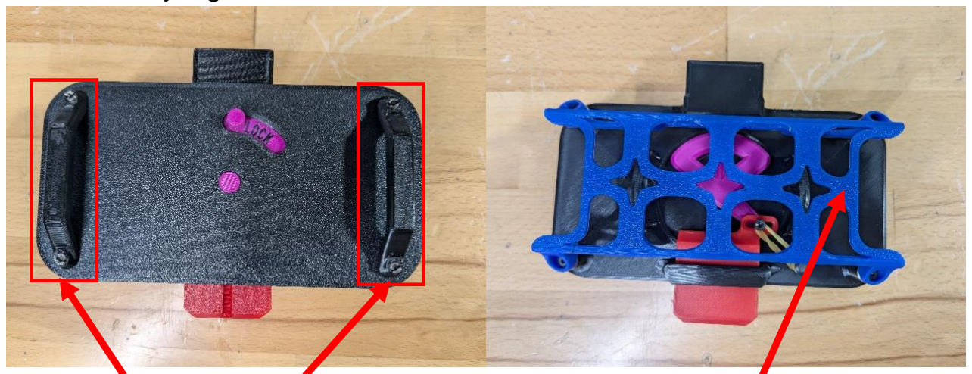
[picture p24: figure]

Handles | Battery cage

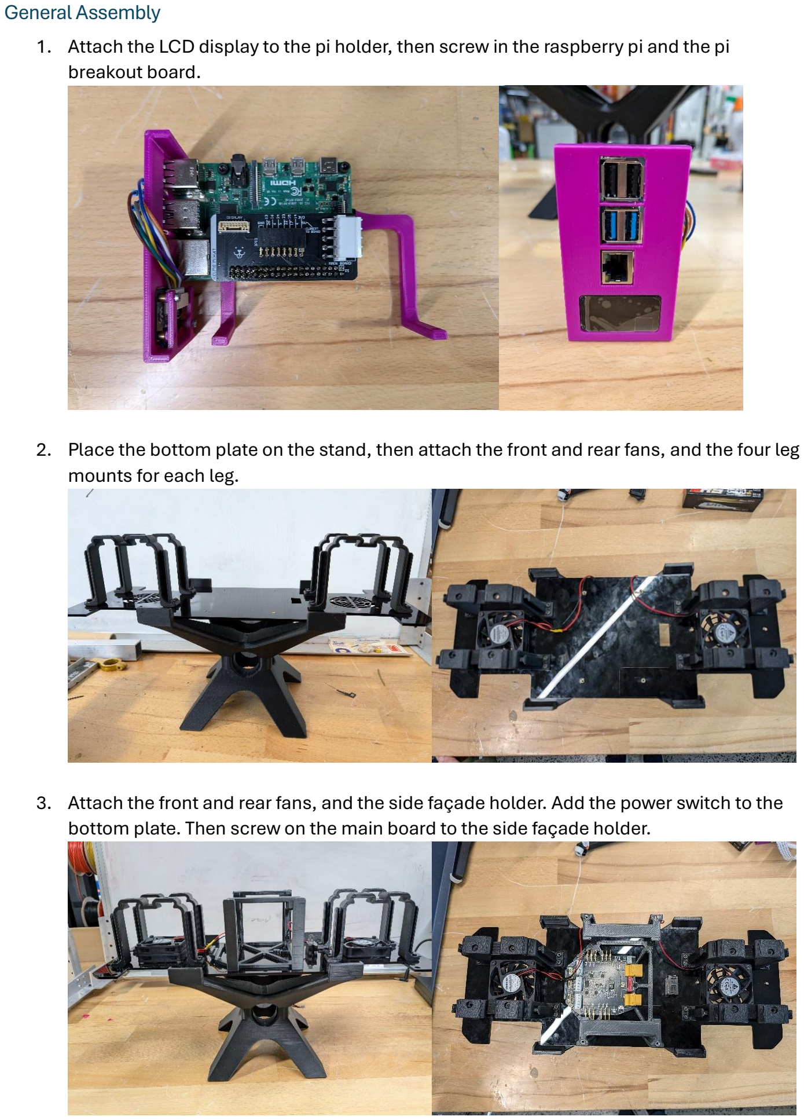
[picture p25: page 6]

General Assembly
1. Attach the LCD display to the pi holder, then screw in the raspberry pi and the pi breakout board.
2. Place the bottom plate on the stand, then attach the front and rear fans, and the four leg mounts for each leg.
3. Attach the front and rear fans, and the side façade holder. Add the power switch to the bottom plate. Then screw on the main board to the side façade holder.

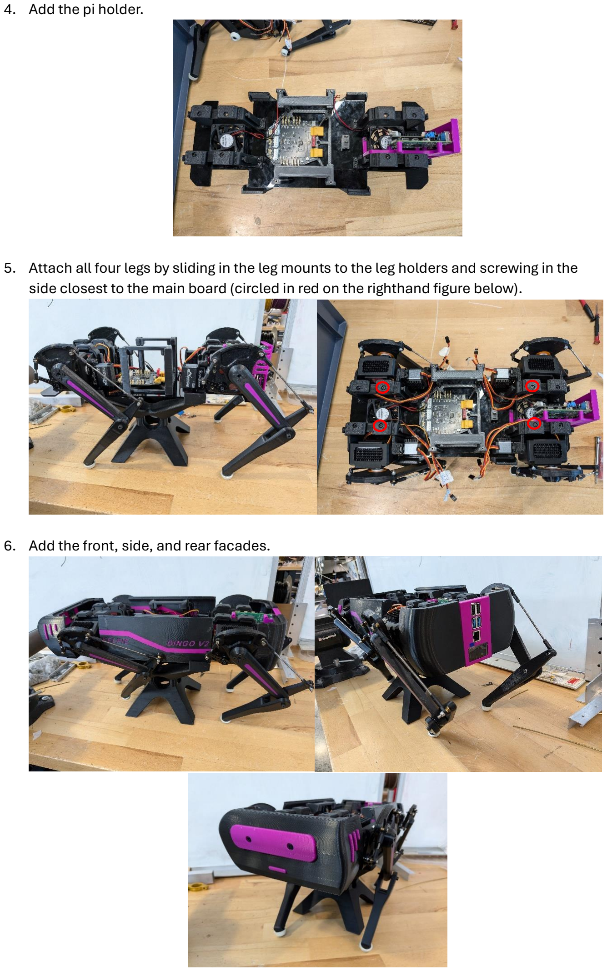
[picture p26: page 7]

4. Add the pi holder.
5. Attach all four legs by sliding in the leg mounts to the leg holders and screwing in the side closest to the main board (circled in red on the righthand figure below).
6. Add the front, side, and rear facades.

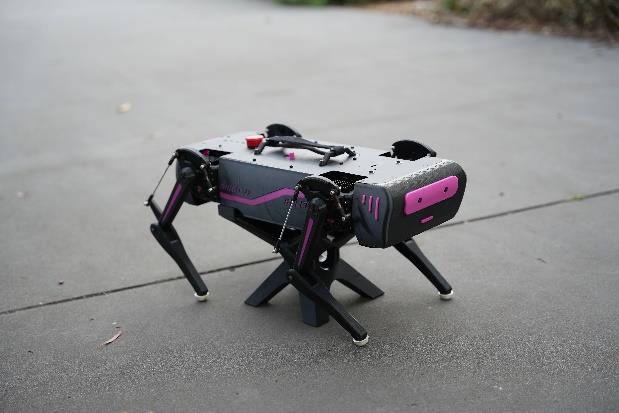
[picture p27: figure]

7. Attach the top plate and insert the battery hatch.

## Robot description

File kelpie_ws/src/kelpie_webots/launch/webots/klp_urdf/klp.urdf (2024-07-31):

<?xml version="1.0" encoding="UTF-8"?>
<robot name="Robot">
    <link name="Base">
        <inertial>
            <mass value="0"/>
            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
        </inertial>
        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
    </link>
    <link name="Body01">
        <inertial>
            <origin rpy="0.00000000 0.00000000 0.00000000" xyz="0.00715934 0.00030873 -0.03703405"/>
            <mass value="0.14865458"/>
            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
        </inertial>
        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
    </link>
    <link name="Body02">
        <inertial>
            <origin rpy="0.00000000 0.00000000 0.00000000" xyz="-0.03312008 -0.00142791 -0.01447259"/>
            <mass value="0.01138778"/>
            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
        </inertial>
        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
    </link>
    <link name="Body03">
        <inertial>
            <origin rpy="0.00000000 0.00000000 0.00000000" xyz="0.04896763 0.04600256 -0.00520000"/>
            <mass value="0.01969612"/>
            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
        </inertial>
        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
    </link>
    <link name="Body04">
        <inertial>
            <origin rpy="0.00000000 0.00000000 0.00000000" xyz="-0.00715934 -0.00030856 -0.03703405"/>
            <mass value="0.14865458"/>
            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
        </inertial>
        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
    </link>
    <link name="Body05">
        <inertial>
            <origin rpy="0.00000000 0.00000000 0.00000000" xyz="-0.03312008 -0.00142791 -0.01447259"/>
            <mass value="0.01138778"/>
            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
        </inertial>
        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
    </link>
    <link name="Body06">
        <inertial>
            <origin rpy="0.00000000 0.00000000 0.00000000" xyz="0.04896763 0.04600256 -0.00520000"/>
            <mass value="0.01969612"/>
            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
        </inertial>
        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
    </link>
    <link name="Body07">
        <inertial>
            <origin rpy="0.00000000 0.00000000 0.00000000" xyz="0.00030881 -0.00715933 -0.03703405"/>
            <mass value="0.14865458"/>
            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
        </inertial>
        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
    </link>
    <link name="Body08">
        <inertial>
            <origin rpy="0.00000000 0.00000000 0.00000000" xyz="-0.00142791 0.03312008 -0.01447259"/>
            <mass value="0.01138778"/>
            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
        </inertial>
        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
    </link>
    <link name="Body09">
        <inertial>
            <origin rpy="0.00000000 0.00000000 0.00000000" xyz="0.06525451 -0.01599730 -0.00520000"/>
            <mass value="0.01969612"/>
            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
        </inertial>
        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
    </link>
    <link name="Body10">
        <inertial>
            <origin rpy="0.00000000 0.00000000 0.00000000" xyz="0.00030831 -0.00715935 -0.03703405"/>
            <mass value="0.14865458"/>
            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
        </inertial>
        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
    </link>
    <link name="Body11">
        <inertial>
            <origin rpy="0.00000000 0.00000000 0.00000000" xyz="-0.00142791 0.03312008 -0.01447259"/>
            <mass value="0.01138778"/>
            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
        </inertial>
        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
    </link>
    <link name="Body12">
        <inertial>
            <origin rpy="0.00000000 0.00000000 0.00000000" xyz="0.06525451 -0.01599730 -0.00520000"/>
            <mass value="0.01969612"/>
            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
        </inertial>
        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
    </link>
    <joint name="Joint01" type="revolute">
        <parent link="Base"/>
        <child link="Body01"/>
        <origin rpy="3.14159265 0.00000000 0.00000000" xyz="0.06500000 0.04800000 0.10250000"/>
        <axis xyz="0.00000000 0.00000000 1.00000000"/>
        <limit lower="-3.14159265" upper="3.14159265" effort="0" velocity="0"/>
    </joint>
    <joint name="Joint02" type="revolute">
        <parent link="Body01"/>
        <child link="Body02"/>
        <origin rpy="-3.14159265 1.57079633 0.00000000" xyz="0.02840000 -0.01310000 -0.02740000"/>
        <axis xyz="0.00000000 0.00000000 1.00000000"/>
        <limit lower="-3.14159265" upper="3.14159265" effort="0" velocity="0"/>
    </joint>
    <joint name="Joint03" type="revolute">
        <parent link="Body02"/>
        <child link="Body03"/>
        <origin rpy="3.14159265 0.00000000 0.00000000" xyz="-0.12990000 0.00000000 -0.02600000"/>
        <axis xyz="0.00000000 0.00000000 1.00000000"/>
        <limit lower="-3.14159265" upper="3.14159265" effort="0" velocity="0"/>
    </joint>
    <joint name="Joint04" type="revolute">
        <parent link="Base"/>
        <child link="Body04"/>
        <origin rpy="0.00000000 0.00000000 3.14159265" xyz="0.06500000 0.04820000 -0.10250000"/>
        <axis xyz="0.00000000 0.00000000 1.00000000"/>
        <limit lower="-3.14159265" upper="3.14159265" effort="0" velocity="0"/>
    </joint>
    <joint name="Joint05" type="revolute">
        <parent link="Body04"/>
        <child link="Body05"/>
        <origin rpy="-3.14159265 -1.57079633 0.00000000" xyz="-0.02720000 -0.01550000 -0.04760000"/>
        <axis xyz="0.00000000 0.00000000 1.00000000"/>
        <limit lower="-3.14159265" upper="3.14159265" effort="0" velocity="0"/>
    </joint>
    <joint name="Joint06" type="revolute">
        <parent link="Body05"/>
        <child link="Body06"/>
        <origin rpy="3.14159265 0.00000000 0.00000000" xyz="-0.12990000 0.00000000 -0.02600000"/>
        <axis xyz="0.00000000 0.00000000 1.00000000"/>
        <limit lower="-3.14159265" upper="3.14159265" effort="0" velocity="0"/>
    </joint>
    <joint name="Joint07" type="revolute">
        <parent link="Base"/>
        <child link="Body07"/>
        <origin rpy="0.00000000 0.00000000 0.00000000" xyz="-0.06500000 0.04800013 -0.10250000"/>
        <axis xyz="0.00000000 0.00000000 1.00000000"/>
        <limit lower="-3.14159265" upper="3.14159265" effort="0" velocity="0"/>
    </joint>
    <joint name="Joint08" type="revolute">
        <parent link="Body07"/>
        <child link="Body08"/>
        <origin rpy="-3.14159265 -1.57079633 0.00000000" xyz="-0.02720000 0.01550000 -0.04760000"/>
        <axis xyz="0.00000000 0.00000000 1.00000000"/>
        <limit lower="-3.14159265" upper="3.14159265" effort="0" velocity="0"/>
    </joint>
    <joint name="Joint09" type="revolute">
        <parent link="Body08"/>
        <child link="Body09"/>
        <origin rpy="3.14159265 0.00000000 0.00000000" xyz="-0.12987943 0.00000000 -0.02600000"/>
        <axis xyz="0.00000000 0.00000000 1.00000000"/>
        <limit lower="-3.14159265" upper="3.14159265" effort="0" velocity="0"/>
    </joint>
    <joint name="Joint10" type="revolute">
        <parent link="Base"/>
        <child link="Body10"/>
        <origin rpy="3.14159265 0.00000000 3.14159265" xyz="-0.06500000 0.04800013 0.10250000"/>
        <axis xyz="0.00000000 0.00000000 1.00000000"/>
        <limit lower="-3.14159265" upper="3.14159265" effort="0" velocity="0"/>
    </joint>
    <joint name="Joint11" type="revolute">
        <parent link="Body10"/>
        <child link="Body11"/>
        <origin rpy="-3.14159265 1.57079633 0.00000000" xyz="0.02840000 0.01310000 -0.02740000"/>
        <axis xyz="0.00000000 0.00000000 1.00000000"/>
        <limit lower="-3.14159265" upper="3.14159265" effort="0" velocity="0"/>
    </joint>
    <joint name="Joint12" type="revolute">
        <parent link="Body11"/>
        <child link="Body12"/>
        <origin rpy="3.14159265 0.00000000 0.00000000" xyz="-0.12987943 0.00000000 -0.02600000"/>
        <axis xyz="0.00000000 0.00000000 1.00000000"/>
        <limit lower="-3.14159265" upper="3.14159265" effort="0" velocity="0"/>
    </joint>
</robot>

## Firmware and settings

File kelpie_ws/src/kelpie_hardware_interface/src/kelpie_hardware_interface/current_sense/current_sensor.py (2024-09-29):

#!/usr/bin/env python

# Written by: William L
# Last Modified 15/08/2024

from barbudor_ina3221.full import *
import board
from enum import IntEnum

from typing import List


class SensorIdx(IntEnum):
    FR = 0
    FL = 1
    RR = 2
    RL = 3


class MotorChan(IntEnum):
    R = 1
    U = 2
    L = 3


class CurrentSensor:
    def __init__(self, addr: int, reg: int, mask: int, value: int,
                 channels: list = (1, 2, 3),
                 shunt_resistor: list = (0.01, 0.01, 0.01)):
        """
        Initialises a new current sensor
        :param addr: Address of the sensor
        :param reg: Register to write too
        :param mask: Masks for bits
        :param value: Values to write
        :param channels: Channels to enable
        :param shunt_resistor: Shunt resistor values in ohm.
        """
        self._current_sensor = INA3221(board.I2C(), i2c_addr=addr, shunt_resistor=shunt_resistor)
        self._current_sensor.update(reg=reg,
                                    mask=mask,
                                    value=value)

        self.channels = channels
        for channel in self.channels:
            self._current_sensor.enable_channel(channel)
            self._current_sensor.enable_channel(channel)
            self._current_sensor.enable_channel(channel)

    @property
    def battery_voltage(self):
        avg = 0
        for channel in self.channels:
            avg += self._current_sensor.bus_voltage(channel) + self._current_sensor.shunt_voltage(channel)

        return avg / len(self.channels)

    @property
    def load_voltage(self):
        avg = 0
        for channel in self.channels:
            avg += self._current_sensor.bus_voltage(channel)

        return avg / len(self.channels)

    def get_current(self, channel: int) -> float:
        return self._current_sensor.current(channel)

    def get_shunt_voltage(self, channel: int) -> float:
        return self._current_sensor.shunt_voltage(channel)


class LegCurrentSensors:
    def __init__(self, fr_addr: int, fl_addr: int, rr_addr: int, rl_addr: int,
                 reg=C_REG_CONFIG,
                 mask=C_AVERAGING_MASK |
                      C_VBUS_CONV_TIME_MASK |
                      C_SHUNT_CONV_TIME_MASK |
                      C_MODE_MASK,
                 value=C_AVERAGING_16_SAMPLES |
                       C_VBUS_CONV_TIME_8MS |
                       C_SHUNT_CONV_TIME_8MS |
                       C_MODE_SHUNT_AND_BUS_CONTINOUS
                 ):
        self._current_sensors: List[CurrentSensor] = [CurrentSensor(fr_addr, reg=reg, mask=mask, value=value),
                                                      CurrentSensor(fl_addr, reg=reg, mask=mask, value=value),
                                                      CurrentSensor(rr_addr, reg=reg, mask=mask, value=value),
                                                      CurrentSensor(rl_addr, reg=reg, mask=mask, value=value)]

    @property
    def battery_voltage(self):
        avg = 0
        for current_sensor in self._current_sensors:
            avg += current_sensor.battery_voltage

        return avg / 4

    @property
    def load_voltage(self):
        avg = 0
        for current_sensor in self._current_sensors:
            avg += current_sensor.load_voltage

        return avg / 4

    @property
    def get_current(self):
        total = 0
        for current_sensor in self._current_sensors:
            for channel in current_sensor.channels:
                total += current_sensor.get_current(channel)

        return total

    def get_shunt_current(self, idx: int, channel: int) -> float:
        return float(self._current_sensors[idx].get_current(channel))

    def get_shunt_voltage(self, idx: int, channel: int) -> float:
        return self._current_sensors[idx].get_shunt_voltage(channel)

if __name__ == '__main__':
    string = "fr u"
    items = string.split(" ")
    print(MotorChan[items[1].upper()].value)

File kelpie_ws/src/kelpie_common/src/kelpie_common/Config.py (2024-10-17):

import math as m

import numpy as np
# from dingo_servo_interfacing.ServoCalibration import MICROS_PER_RAD, NEUTRAL_ANGLE_DEGREES
from kelpie_hardware_interface.handheld_controller.Ps4Config import PS4_COLOR, PS4_DEACTIVATED_COLOR
from enum import Enum


class Configuration:
    def __init__(self):
        ################# CONTROLLER BASE COLOR ##############
        self.ps4_color = PS4_COLOR
        self.ps4_deactivated_color = PS4_DEACTIVATED_COLOR

        #################### COMMANDS ####################
        self.max_x_velocity = 1
        self.max_y_velocity = 0.5
        self.y_vel_tf = lambda y: y * 1  # Allow arbitrary transformation function to be applied to controller inputs
        self.x_vel_tf = lambda x: x * 1  # Allow arbitrary transformation function to be applied to controller inputs

        # TODO: Tune max yaw rate. Right now it is too fast for the dog to react in sim.
        self.max_yaw_rate = 2
        self.max_pitch = 15.0 * np.pi / 180.0

        #################### MOVEMENT PARAMS ####################
        self.z_time_constant = 0.02
        self.z_speed = 0.06  # maximum speed [m/s]
        self.pitch_deadband = 0.05
        self.pitch_time_constant = 0.25
        self.max_pitch_rate = 1
        self.roll_speed = 1  # maximum roll rate [rad/s]
        self.yaw_time_constant = 0.3
        self.max_stance_yaw = 0.8
        self.max_stance_yaw_rate = 1

        #################### STANCE ####################
        self.delta_x = 0.117  # - 0.00535 #115650.00535

        # These x_shift variables will move the default foot positions of the robot
        # Handy if the centre of mass shifts as can move the feet to compensate
        self.rear_leg_x_shift = 0.00  # In default config, the robots mass is slightly biased to the back feet, so the back feet are shifted back slightly
        self.front_leg_x_shift = 0.05

        self.delta_y = 0.1106  # 0.1083
        self.default_z_ref = -0.25  # -0.16

        #################### SWING ######################
        self.z_coeffs = None
        self.z_clearance = 0.08
        self.alpha = (
            0.7  # Ratio between touchdown distance and total horizontal stance movement
        )
        self.beta = (
            0.5  # Ratio between touchdown distance and total horizontal stance movement
        )

        #################### GAIT #######################
        self.dt = 0.01
        self.num_phases = 4
        self.contact_phases = np.array(
            [[1, 1, 1, 0], 
             [1, 0, 1, 1], 
             [1, 0, 1, 1], 
             [1, 1, 1, 0]]
        )
        self.overlap_time = (
            0.04  # duration of the phase where all four feet are on the ground
        )
        self.swing_time = (
            0.07  # duration of the phase when only two feet are on the ground
        )

        ######################## GEOMETRY ######################
        self.LEG_FB = 0.14  # front-back distance from center line to leg axis
        self.LEG_LR = 0.065  # left-right distance from center line to leg plane
        self.LEG_ORIGINS = np.array(  # Origins of the initial frame from the centre of the body
            [
                [self.LEG_FB, self.LEG_FB, -self.LEG_FB, -self.LEG_FB],
                [-self.LEG_LR, self.LEG_LR, -self.LEG_LR, self.LEG_LR],
                [0, 0, 0, 0],
            ]
        )

        # Leg lengths
        self.L1 = 0.05162024721
        self.L2 = 0.130
        self.L3 = 0.13813664159 + 0.03
        self.phi = m.radians(73.91738698)

        ################### INERTIAL ####################
        self.FRAME_MASS = 0.560  # kg
        self.MODULE_MASS = 0.080  # kg
        self.LEG_MASS = 0.030  # kg
        self.MASS = self.FRAME_MASS + (self.MODULE_MASS + self.LEG_MASS) * 4

        # Compensation factor of 3 because the inertia measurement was just
        # of the carbon fiber and plastic parts of the frame and did not
        # include the hip servos and electronics
        self.FRAME_INERTIA = tuple(
            map(lambda x: 3.0 * x, (1.844e-4, 1.254e-3, 1.337e-3))
        )
        self.MODULE_INERTIA = (3.698e-5, 7.127e-6, 4.075e-5)

        leg_z = 1e-6
        leg_mass = 0.010
        leg_x = 1 / 12 * self.L2 ** 2 * leg_mass
        leg_y = leg_x
        self.LEG_INERTIA = (leg_x, leg_y, leg_z)

    @property
    def default_stance(self):  # Default stance of the robot relative to the centre frame
        return np.array(
            [
                [
                    self.delta_x + self.front_leg_x_shift,  # Front Right
                    self.delta_x + self.front_leg_x_shift,  # Front Left
                    -self.delta_x + self.rear_leg_x_shift,  # Back Right
                    -self.delta_x + self.rear_leg_x_shift,  # Back Left
                ],
                [-self.delta_y, self.delta_y, -self.delta_y, self.delta_y],
                [0, 0, 0, 0],
            ]
        )
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

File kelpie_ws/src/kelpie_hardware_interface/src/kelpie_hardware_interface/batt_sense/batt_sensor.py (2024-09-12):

import board
import busio
from adafruit_tla202x import TLA2024

class BattVSensor:
    def __init__(self, addr: int = 0x48):
        i2c = busio.I2C(board.SCL, board.SDA)
        self.tla = TLA2024(i2c, address=addr)

    @property
    def v0(self):
        self.tla.input_channel = 0
        return self.tla.voltage

    @property
    def v1(self):
        self.tla.input_channel = 1
        return self.tla.voltage

    @property
    def v2(self):
        self.tla.input_channel = 2
        return self.tla.voltage

    @property
    def v3(self):
        self.tla.input_channel = 3
        return self.tla.voltage

    @property
    def v0_batt(self):
        """
        Assumes direct battery cell voltage
        """
        return self.v0

    @property
    def v1_batt(self):
        """
        Assumes resistor divider for half cell voltage
        """
        V0 = self.v0
        v1 = self.v1
        return 2 * v1 - V0

    @property
    def v2_batt(self):
        """
        Assumes resister divider for 1/3 cell voltage
        """
        V0 = self.v0
        V1 = self.v1_batt
        v2 = self.v2
        return 3 * v2 - V1 - V0

    @property
    def v3_batt(self):
        """
        Assumes resistor divider for 1/4 cell voltage
        """
        V0 = self.v0
        V1 = self.v1_batt
        V2 = self.v2_batt
        v3 = self.v3
        return 4 * v3 - V2 - V1 - V0


if __name__ == '__main__':
    bs = BattVSensor()
    print(f"V0_batt: {bs.v0_batt}, V1_batt: {bs.v1_batt}\nV0_raw: {bs.v0}, V1_raw: {bs.v1}\nV2_raw: {bs.v2*2}")

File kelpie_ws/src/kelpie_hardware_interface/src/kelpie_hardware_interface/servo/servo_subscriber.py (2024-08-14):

#!/usr/bin/env python
import os
import numpy as np
import rospy
from kelpie.msg import leg_state, joint_states
from kelpie_hardware_interface.servo.Interface import ServoInterface
from kelpie_common.Config import Leg_linkage, Configuration

class ServoSubscriber:
    def __init__(self):
        self.servo_interface = ServoInterface(Leg_linkage(Configuration()))
        rospy.Subscriber("/kelpie/leg_control/joint_states", joint_states, self.callback)
        print("started")

    def callback(self, data):
        joint_angles = self.convert_to_array(data)
        self.servo_interface.set_actuator_postions(joint_angles)

    @staticmethod
    def convert_to_array(data):
        joint_angles = np.zeros((3, 4))
        joint_angles[:, 0] = data.fr.roll, data.fr.upper, data.fr.lower
        joint_angles[:, 1] = data.fl.roll, data.fl.upper, data.fl.lower
        joint_angles[:, 2] = data.rr.roll, data.rr.upper, data.rr.lower
        joint_angles[:, 3] = data.rl.roll, data.rl.upper, data.rl.lower
        return joint_angles

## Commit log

2024-04-01 intial branch cleanup (delete v1 stuff)
    [Bill of Materials-Dingo_PCB.xlsx, Dingo Robot Bill of Materials.xlsx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]
2024-04-01 add folder strucutre for pcb
2024-04-03 made significant progress to servoboard
    [Dingo_ServoBoard.PrjPcb, ServoBoard_Schematic.SchDoc]
2024-04-03 readd assets folder for a pretty readme
    [ServoBoard_Schematic.SchDoc]
2024-04-03 Adding in initial files
    [Kelpie_PDB.PrjPcb]
2024-04-03 Made 5v buck
    [Kelpie_PDB.PrjPcb, PDB_schematic.SchDoc]
2024-04-03 finish servoboard schematic; add header
    [Dingo_ServoBoard.PrjPcb, ServoBoard_Schematic.SchDoc]
2024-04-03 Added in voltage monitoring
    [Kelpie_PDB.PrjPcb, PDB_schematic.SchDoc]
2024-04-04 Fixed ordering of balance lead
    [PDB_schematic.SchDoc]
2024-04-04 Added in XT60
    [PDB_schematic.SchDoc]
2024-04-06 add ppulldown to i2c addy line
    [ServoBoard_Schematic.SchDoc]
2024-04-06 added ltspice sim for battery mon
2024-04-08 Added 7.4V Rail Reg
    [PDB_schematic.SchDoc]
2024-04-08 fix mistakes in servo schematic
    [ServoBoard_Schematic.SchDoc]
2024-04-08 Added i2c splitter
    [PDB_schematic.SchDoc]
2024-04-09 fix disconnected wire
    [PDB_schematic.SchDoc]
2024-04-13 Added comp to boards
    [Kelpie_PDB.PrjPcb, PDB.PcbDoc, PDB_lib.PcbLib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]
2024-04-13 Fixed rules
    [PDB.PcbDoc, ServoBoard.PcbDoc, ServoBoard.~(3).PcbDoc]
2024-05-15 add final main board v1
    [0805L002YR_0805L002YR.x_t, 1x3_Dupont_1x3_dupont.x_t, 3587TR_3587TR.x_t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]
2024-07-15 Worked on propagating servo angles to feet angles, and reversing that calculation. This will be useful for forwards kinematics, and maybe the inverse too.
2024-07-20 klp_urdf
    URDF no limits initial push
    [Body01.stl, Body01_coll.stl, Body02.stl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]
2024-07-30 Pushed webot stuff
    [Body01.stl, Body01_coll.stl, Body02.stl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]
2024-07-30 - Fixed scaling - Moved kelpie_webots into dingo_ws - Made launch file
    [Body01.stl, Body01_coll.stl, Body02.stl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]
2024-07-31 Rearranged files for ROS1. Added in joint names to each joint in klp.proto Added in run file for PyCharm Added in webots_launcher.py
    [Body01.stl, Body01_coll.stl, Body02.stl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]
2024-07-31 Changed scaling of stl files and fixed incorrect urdf/proto lower leg alignments.
    [Body01.stl, Body01_coll.stl, Body02.stl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]
2024-08-01 -Added in kelpie workspace and set up the joint state publishing.
    -Set up subscribing from the SIM.
    [Body01.stl, Body01_coll.stl, Body02.stl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]
2024-08-05 Fixed mapping for the robot leg angles in webot simulation
2024-08-06 Fixed naming error in config file
    [Config.py]
2024-08-06 Moved servo controller to hardware node
2024-08-09 - Fixed joystick input scaling. - Added in the ability to apply a transfer fucntion to joystick input.
    [Config.py]
2024-08-09 Commit from dingo
    [Body01.stl, Body01_coll.stl, Body02.stl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]
2024-08-11 - Renamed folders - Added in IMU sensors to Webots and associated publisher and subscriber - Added in messages for imu nodes
    [Body01_coll.stl, Body02_coll.stl, Body03_coll.stl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]
2024-08-11 - Added in calibrate.py - Added in current_sensor.py - Added in imu_balancer.py - Added in motor_current_subscriber.py - Minor type hinting changes
2024-08-11 - Refactored servo control into own class. - Added in TODO's
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2024-08-14 servo calibration scripts
    [calibrate_servo_angles.yaml, calibrate_servo_angles_BACKUP.yaml]
2024-08-14 - Added in current sensor code - Minor refactoring of ps5.py
2024-08-14 - Fixed calibrate_servo.py initial offset values.
    [calibrate_servo.py]
2024-08-14 - Added in current reporting in calibration script.
2024-08-15 - Added in matlab torque calculations.
2024-08-28 - Added in IMU calibration settling script.
2024-08-30 Started current sensor calibration
2024-08-30 push from pi
    [calibrate_servo_angles.yaml]
2024-08-30 Added in current publishing
2024-08-31 - Enabled IMU balance from webots. Changed how the code is done (No change to logic) for organisation.
2024-09-04 add in imu submodule
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2024-09-05 udpate sensor fusion in module
2024-09-06 - Added in sensor fusion enable code. Need to do sensor fusion reading code.
2024-09-08 Changed sensor read for quaternion in imu_test.py
2024-09-08 - Added in other sensor fusion batch settings and their relative getters and setters.
2024-09-08 - Fixed mem bank access
    [LSM6DSV16X_imu_test.py]
2024-09-08 Changed printing to suit floats rather than int
2024-09-09 Added voltage monitor script
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2024-09-09 Updated README for voltage monitoring, and added initial test for LCD screen
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2024-09-10 - Changed gyro to gyroscope, changed acceleration to accelerometer - Added in skeleton code for quaternion processing. - Progressed further in IMU publisher (Waiting on quaternion processing)
2024-09-10 - Small bug fix and refactoring. - Added in some docstrings.
    [LSM6DSV16X_imu_test.py]
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2024-09-10 edit files to get ros nodes to run error free; calibrate dog
    [calibrate_servo_angles.yaml]
2024-09-11 Added in calibrate functions to do all legs.
2024-09-11 Minor bug fix with order of functions.
    [calibrate_servo.py]
2024-09-11 Added in current calibration. -Will
    [calibrate_servo_angles.yaml, calibrate_servo_angles_BACKUP.yaml]
2024-09-12 Fixed calibration script not returning values.
    [Utilities.py, calibrate_servo.py, current_sensor_calibrate.py]
2024-09-12 Fixed auto calibration with problem with roll -will Got html working -cian
    [calibrate_servo_angles.yaml]
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2024-09-12 IMU bug fix in publisher.
    [LSM6DSV16X_imu_test.py, publisher.py]
2024-09-13 Fixed bug in ROS by renaming message name.
    [calibrate_servo_angles.yaml]
2024-09-13 Added in step by step thoughts for IMU cal
2024-09-15 - Added in PID controlled roll pitch and yaw, based of IMU SFLP. This should achieve a naive balance controller.
    - Fixed webots translation layer mapping wrong IMU outputs.
    - Refactored command handling to be in controller.py rather than command_input_subscriber.py.
    - Created new state handling mechanism
    [Config.py, Utilities.py]
2024-09-15 - Added button to toggle PID on and off. By default PID is disabled. Press Square to toggle.
2024-09-16 udpate to non-cooked cal
    [calibrate_servo_angles.yaml]
2024-09-16 Fixed roll and pitch imu balancer.
    [calibrate_servo_angles.yaml]
2024-09-16 Push from dingo. Fixing balancer code for trotting.
    [Config.py]
2024-09-16 Modified js script to display all leg status
2024-09-16 - Removed rolling average on yaw control when in trot mode.
2024-09-17 update web server
    [calibrate_servo_angles.yaml]
2024-09-24 - Fixed rapid pitch input.
    [publisher.py]
2024-09-24 Fixed main driver bug -will
    [calibrate_servo_angles.yaml]
2024-09-24 PID tuned with ziegler nicholas and fixed state estimation bug -will
    [Config.py]
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2024-09-25 - Fixed battery relative import
    [Config.py, LCD_1inch47.py, batt_displayer.py]
2024-09-25 -Renamed vec3d_float32.msg to vec_xyz_float32.msg due to ROS bug?
    [LSM6DSV16X_imu_test copy.py, publisher.py]
2024-09-25 - Fixing bug from ROS
    [LSM6DSV16X_imu_test copy.py, publisher.py]
2024-09-25 Added in camera dependencies and ros network change.
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2024-09-25 Added in camera node and added in display code.
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2024-09-27 upload PCB files, remove unused v1 files
    [0805L002YR_0805L002YR.x_t, 1x3_Dupont_1x3_dupont.x_t, 3587TR_3587TR.x_t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]
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2024-09-28 - Fixed walking
    [calibrate_servo_angles.yaml]
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2024-09-28 Fixed yaw control
2024-09-29 - Added PS5 controller profile (WIP) - Tuned some gait params in Config.py - Reduced I2C read as it was causing large delays in response - Fixed bugs in stance and swing leg controller that was resul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
    [Config.py]
2024-09-29 - Fixed wrong current sensor shunt resistor value.
    [current_sensor.py, current_sensor_calibrate.py]
2024-10-14 fixed logger code (Will), added auto display (Cian)
    [20241014-185228.csv, calibrate_servo_angles.yaml]
2024-10-14 Added in notebook for plotting data
    [20241014-185228.csv]
2024-10-14 stop commiting pesky log files
    [20241014-185228.csv]
2024-10-15 Data logged for PID and trotting.
    [20241015-152325.csv]
2024-10-17 -Added in IMU notebook for plotting data to do with step responses.
2024-10-17 - Added in code and notebook that generates and displays workspace boundaries.
    [workspace_boundary_gen.csv]
2024-10-18 - Implemented workspace boundaries - Fixed up the launch files
    [20241015-152325.csv, workspace_boundaries.csv, workspace_boundary_gen.csv]
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2024-10-18 Added docs and renamed folder names for consistency
    [kelpie_BOM.xlsx]
2024-10-18 - Read me changes -Unmapping calibration button - Image changes
